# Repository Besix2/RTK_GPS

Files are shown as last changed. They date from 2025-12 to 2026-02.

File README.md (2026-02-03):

# RTK_GPS
A RTK GPS sensor Board for drones based around the Quectel LC29H Chip. It should offer accuracy of up to 5cm. It needs a Basestation or (depending on your country) position correcting GPS data that is send to the esp32.

For a more detailed write up you can check out the journal at [Blueprint](https://blueprint.hackclub.com/projects/7904).

## Why?
I made the project because I wanted to develop a drone and needed high precission and noticed that any available solutions are insanly expensive, so I came up with my own design.

## How?
I researched several different types of drone positioning systems and basically every professional use case uses RTK GPS due to its unmatched precission. I researched multiple RTK GPS modules and found none that were cheap enough/could do what I needed. So after a lot of researching I stumbled upon the quectel LC29H module that could everything I needed. It only needed some sort of correction data. I discovered that my country offers correction data via the internet so I just needed a way to serve this data to the modul over tha air. For that I decided to use an ESP32 as it already has native support for these kind of data transmissions by ardupilot. Because this arrangement needs some resistors and capacitors I designed my own Pcb.
grafik

grafik

grafik

grafik

grafik

| Designator | Value | Footprint | Quantity | Price | Link | Total Price |
|:---|:---|:---|---:|---:|:---|---:|
| C4, C5, C6 | 10uF | 603 | 3 | 0.15 | JLCPCB Part | 0.45 |
| C7 | 100nF | 603 | 1 | 0.05 | JLCPCB Part | 0.05 |
| D1 | LED | 603 | 1 | 0.05 | JLCPCB Part | 0.05 |
| R1, R2, R5 | 10k | 603 | 3 | 0.1  | JLCPCB Part | 0.3  |
| J5 | Conn_01x04_Socket | PinHeader_1x04_P2.54mm | 1 | 0.2  | JLCPCB Part | 0.2  |
| SW1, SW2 | SW_Push | SW_SPST_B3S-1000 | 2 | 0.3  | JLCPCB Part | 0.6  |
| U1 | ESP32-WROOM-32E | ESP32-WROOM-32E | 1 | 3.5  | JLCPCB Part | 3.5  |
| U3 | AMS1117-3.3 | SOT-223-3 | 1 | 0.25 | JLCPCB Part | 0.25 |
| GPS Antenna | Helix Ceramic RTK Dual Band | External | 1 | 13.59 | [Link](https://de.aliexpress.com/item/1005009918181431.html) | 13.59 |
| GPS Connector  | Generic Connector | External | 1 | 1.65 | [Link](https://de.aliexpress.com/item/1005005073187553.html) | 1.65 |
| Compass (U2?)  | QMC5583L | Module | 1 | 1.89 | [Link](https://de.aliexpress.com/item/1005006794324860.html) | 1.89 |
| ELRS Module | Onboard Antenna | Module | 1 | 7.69 | [Link](https://de.aliexpress.com/item/1005005236594556.html) | 7.69 |
| Cables AWG28 | Silicone Cable | Wiring | 1 | 5.59 | [Link](https://de.aliexpress.com/item/1005007671008743.html) | 5.59 |
| Cables AWG24 | Silicone Cable | Wiring | 1 | 7.89 | [Link](https://de.aliexpress.com/item/1005006350734418.html) | 7.89 |
| FC | SpeedyBee F405 V3 | Fc | 1 | 39.39 | [Link](https://de.aliexpress.com/item/1005004868739263.html) | 39.39 |
| RTK GPS Module | Quectel LC29H (HDA) | Module | 1 | 23.59 | [Link](https://de.aliexpress.com/item/1005006870751088.html) | 23.59 |

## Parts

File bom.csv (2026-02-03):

Designator | Value | Footprint | Quantity | Price | Link | Total Price
C4, C5, C6 | 10uF | 603 | 3 | 0.15 | JLCPCB Part | 0.44
C7 | 100nF | 603 | 1 | 0.05 | JLCPCB Part | 0.05
D1 | LED | 603 | 1 | 0.05 | JLCPCB Part | 0.05
R1, R2, R5 | 10k | 603 | 3 | 0.1 | JLCPCB Part | 0.3
J5 | Conn_01x04_Socket | PinHeader_1x04_P2.54mm | 1 | 0.2 | JLCPCB Part | 0.2
SW1, SW2 | SW_Push | SW_SPST_B3S-1000 | 2 | 0.3 | JLCPCB Part | 0.6
U1 | ESP32-WROOM-32E | ESP32-WROOM-32E | 1 | 3.5 | JLCPCB Part | 3.5
U3 | AMS1117-3.3 | SOT-223-3 | 1 | 0.25 | JLCPCB Part | 0.25
GPS Antenna | Helix Ceramic RTK Dual Band | External | 1 | 13.59 | https://de.aliexpress.com/item/1005009918181431.html | 13.59
GPS Connector | Generic Connector | External | 1 | 1.65 | https://de.aliexpress.com/item/1005005073187553.html | 1.65
Compass | QMC5583L | Module | 1 | 1.89 | https://de.aliexpress.com/item/1005006794324860.html | 1.89
ELRS Module | Onboard Antenna | Module | 1 | 7.69 | https://de.aliexpress.com/item/1005005236594556.html | 7.69
Cables AWG28 | Silicone Cable | Wiring | 1 | 5.59 | https://de.aliexpress.com/item/1005007671008743.html | 5.59
Cables AWG24 | Silicone Cable | Wiring | 1 | 7.89 | https://de.aliexpress.com/item/1005006350734418.html | 7.89
FC | SpeedyBee F405 V3 | Stack | 1 | 39.39 | https://de.aliexpress.com/item/1005004868739263.html | 39.39
RTK GPS Module | Quectel LC29H (HDA) | Module | 1 | 23.59 | https://de.aliexpress.com/item/1005006870751088.html | 23.59

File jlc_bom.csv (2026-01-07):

Designator | Footprint | Quantity | Value | LCSC Part #
C4, C5, C6 | 0603 | 3 | 10µF
C7 | 0603 | 1 | 100nF
D1 | 0603 | 1 | LED
J1 | PinHeader_1x07_P2.54mm_Vertical | 1 | Conn_01x07_Socket
J3, J5 | PinHeader_1x04_P2.54mm_Vertical | 2 | Conn_01x04_Socket
J4 | PinHeader_1x05_P2.54mm_Vertical | 1 | Conn_01x05_Socket
J6 | PinHeader_2x05_P2.54mm_Vertical | 1 | Conn_02x05_Top_Bottom
R1, R2, R5 | 0603 | 3 | 10k
SW1, SW2 | SW_SPST_B3S-1000 | 2 | SW_Push
U1 | ESP32-WROOM-32E | 1 | ESP32-WROOM-32E
U3 | SOT-223-3_TabPin2 | 1 | AMS1117-3.3

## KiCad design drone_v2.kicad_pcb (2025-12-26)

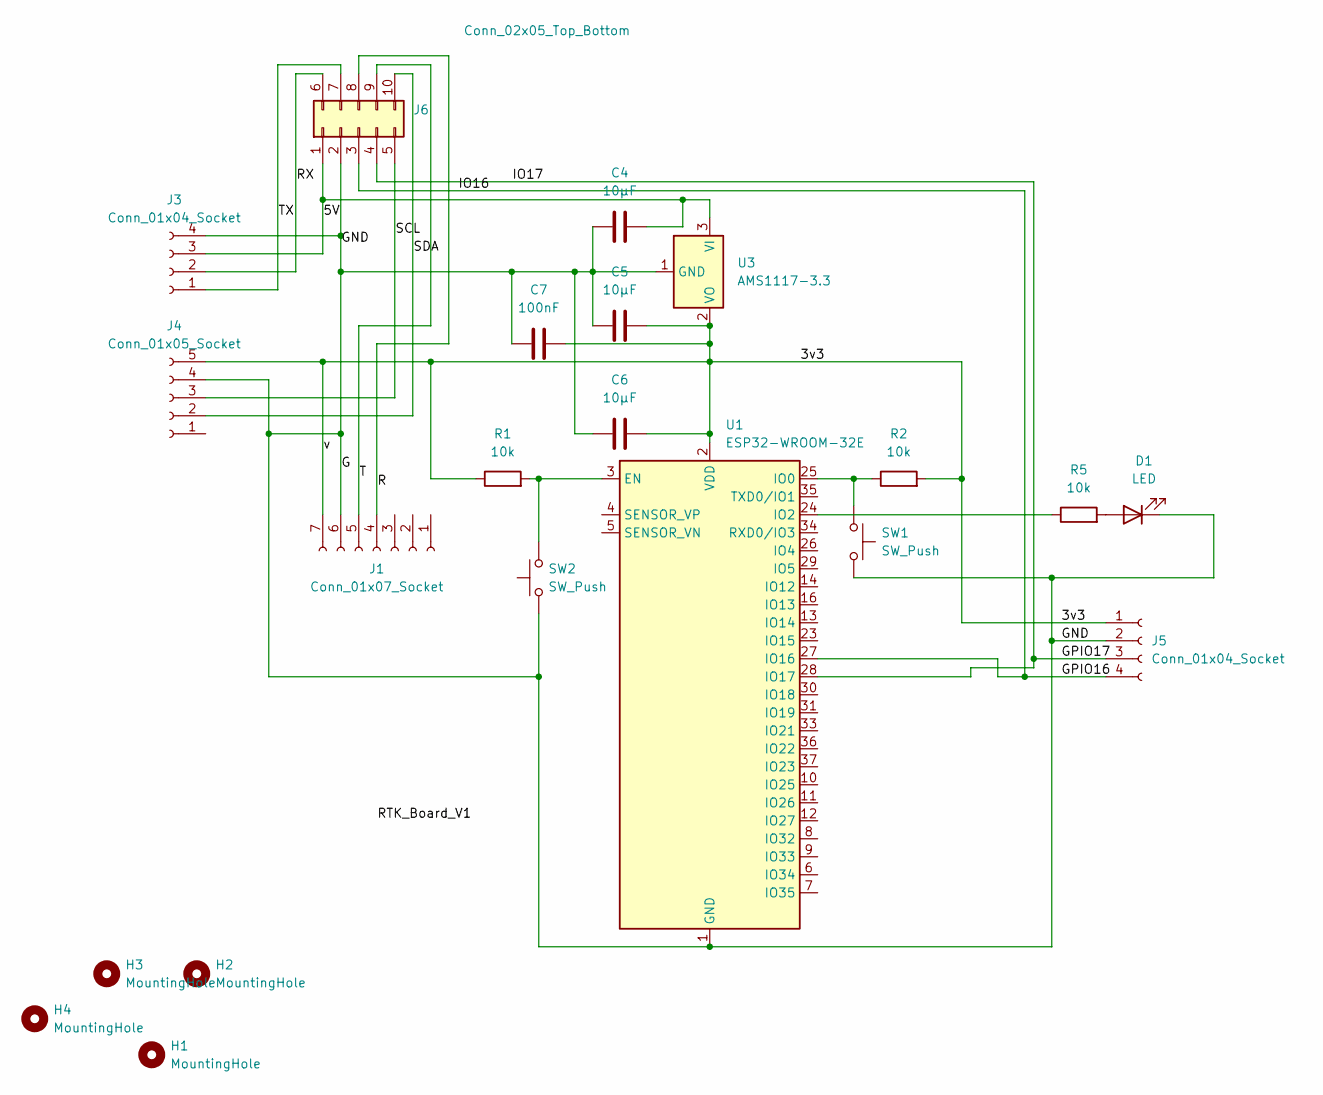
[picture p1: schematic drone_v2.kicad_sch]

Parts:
C4, C5, C6: 10µF; C_0603_1608Metric
C7: 100nF; C_0603_1608Metric
D1: LED; LED_0603_1608Metric
H1, H2, H3, H4: MountingHole; MountingHole_2.2mm_M2
J1: Conn_01x07_Socket; PinHeader_1x07_P2.54mm_Vertical
J3, J5: Conn_01x04_Socket; PinHeader_1x04_P2.54mm_Vertical
J4: Conn_01x05_Socket; PinHeader_1x05_P2.54mm_Vertical
J6: Conn_02x05_Top_Bottom; PinHeader_2x05_P2.54mm_Vertical
R1, R2, R5: 10k; R_0603_1608Metric
SW1, SW2: SW_Push; SW_SPST_B3S-1000
U1: ESP32-WROOM-32E
U3: AMS1117-3.3; SOT-223-3_TabPin2

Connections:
/3v3: C5.2, C6.2, C7.2, J1.7, J4.5, J5.1, R1.1, R2.2, U1.2 (VDD), U3.2 (VO)
/5V: C4.2, J3.3, J6.1, U3.3 (VI)
/G: C4.1, C5.1, C6.1, C7.1, D1.1 (K), J1.6, J3.4, J4.4, J5.2, J6.2, SW1.2, SW2.1, U1.1 (GND), U1.15 (GND), U1.38 (GND), U1.39 (GND), U3.1 (GND)
/GPIO16: J5.4, J6.3, U1.27 (IO16)
/GPIO17: J5.3, J6.4, U1.28 (IO17)
/R: J1.4, J6.8
/RX: J3.2, J6.6
/SCL: J4.3, J6.5
/SDA: J4.2, J6.10
/T: J1.5, J6.9
/TX: J3.1, J6.7
unnamed: D1.2 (A), R5.2
unnamed: R1.2, SW2.2, U1.3 (EN)
unnamed: R2.1, SW1.1, U1.25 (IO0)
unnamed: R5.1, U1.24 (IO2)

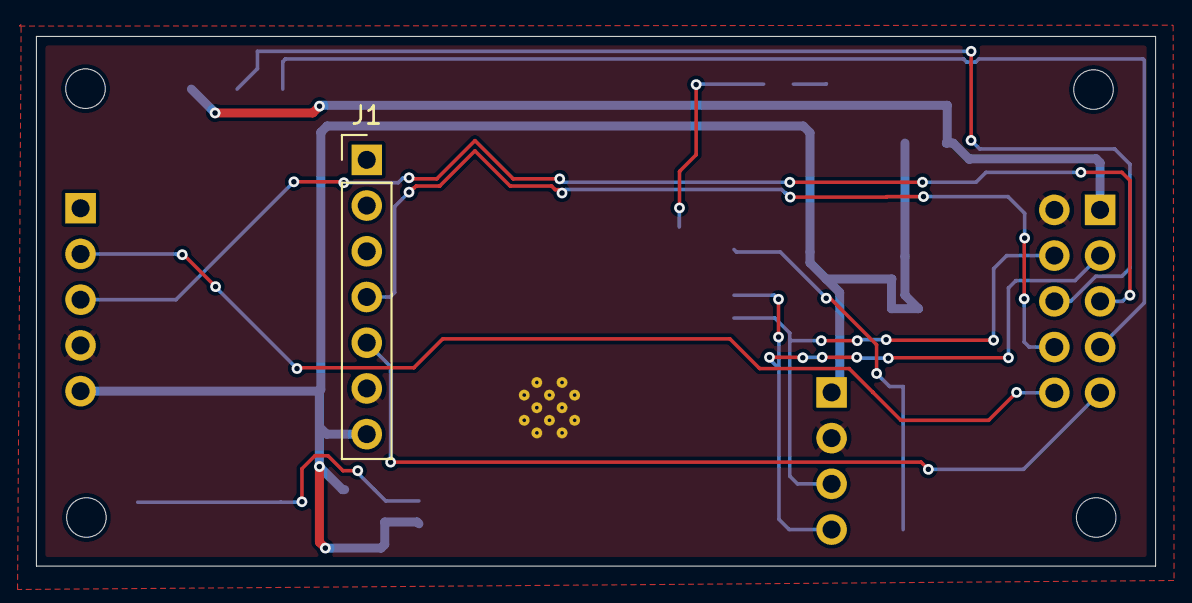
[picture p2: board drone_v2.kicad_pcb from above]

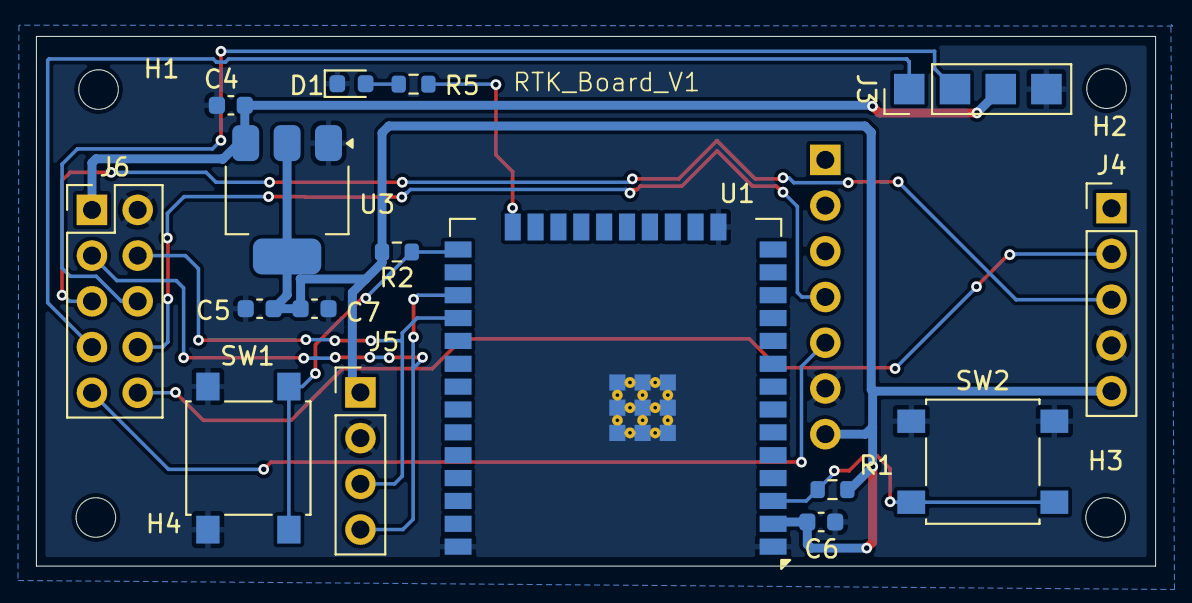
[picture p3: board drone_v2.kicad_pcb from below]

Board: 2 copper layers, 62.2 x 29.4 mm, 21 parts (16 on the bottom side), 15 nets.

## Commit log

2025-12-26 Add dummy file in Gerber directory
2025-12-28 Enhance README with detailed sensor information
    Updated project description to include details about the Quectel LC29H Chip and accuracy specifications.
2026-01-21 Update and rename bom.csv to ki_cad_bom.csv
    [ki_cad_bom.csv]
2026-02-01 Fix header format and spacing in bom.csv
    Updated the header format and corrected spacing in bom.csv.
    [bom.csv]
2026-02-01 Update bom.csv formatting and component values
    [bom.csv]
2026-02-03 Update and rename ki_cad_bom.csv to jlc_bom.csv
    [jlc_bom.csv]
2026-02-03 Update BOM file with component details
    Updated the BOM file to reflect changes in component details.
    [bom.csv]
